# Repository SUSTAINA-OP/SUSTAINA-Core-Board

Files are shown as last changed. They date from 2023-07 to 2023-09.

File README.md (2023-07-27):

<html lang="en">

<head>
	<meta charset="uft-8">
	<meta name="author" content="Masato Kubotera">
    <meta name="description" content="">
</head>

<body>
    <p><strong>This product is currently under development!</strong></p>
	<h1>SUSTAINA Core Board</h1>
        <p>
			This product is the core electronic board of the open hardware platform humanoid robot SUSTAINA-OP<sup>TM</sup>.
			This product requires multiple modules(4 x <a href="https://github.com/SUSTAINA-OP/Power-Monitor-Module">Power Monitor Module</a> and 1 x <a href="https://github.com/SUSTAINA-OP/Buck-Boost-Switch-Mode-Power-Supply-Module">Buck-Boost Switch Mode Power Supply Module</a>) to work. The board automatically selects a priority power source from two battery inputs within the operating voltage range to supply various devices. The power input and output are equipped with short-circuit protection circuits using fuses. In addition, the battery input has multiple MOSFETs to prevent reverse connection and reverse current. The power supply to the actuator and single-board computer can be turned on and off with the load switch circuit.<br>
			<br>
			Rev. 1 of this product is used by <a href="https://github.com/citbrains">CIT Brains</a>, a participant in RoboCup2023 Soccer Humanoid League KidSize.
        </p>
	<h2>Features Rev. 1</h2>
        <p>
            <table>
                <tr>
                    <th>Top Surface of PCB</th>
                    <th>Bottom Surface of PCB</th>
                    <th>Assembled Electronic Components</th>
                </tr>
                <tr>
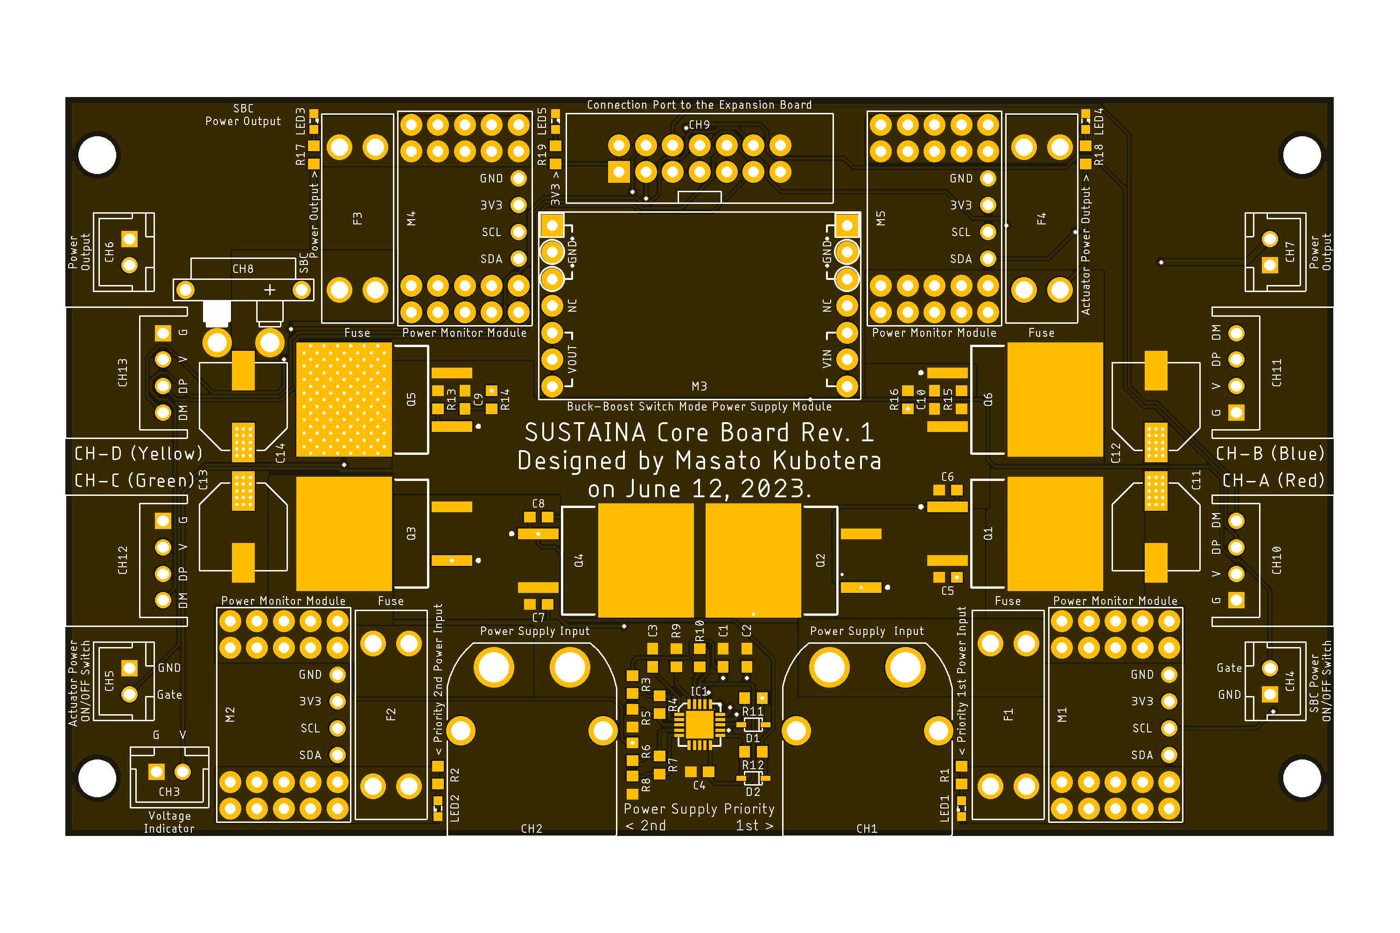
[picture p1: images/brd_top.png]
                    <td></td>
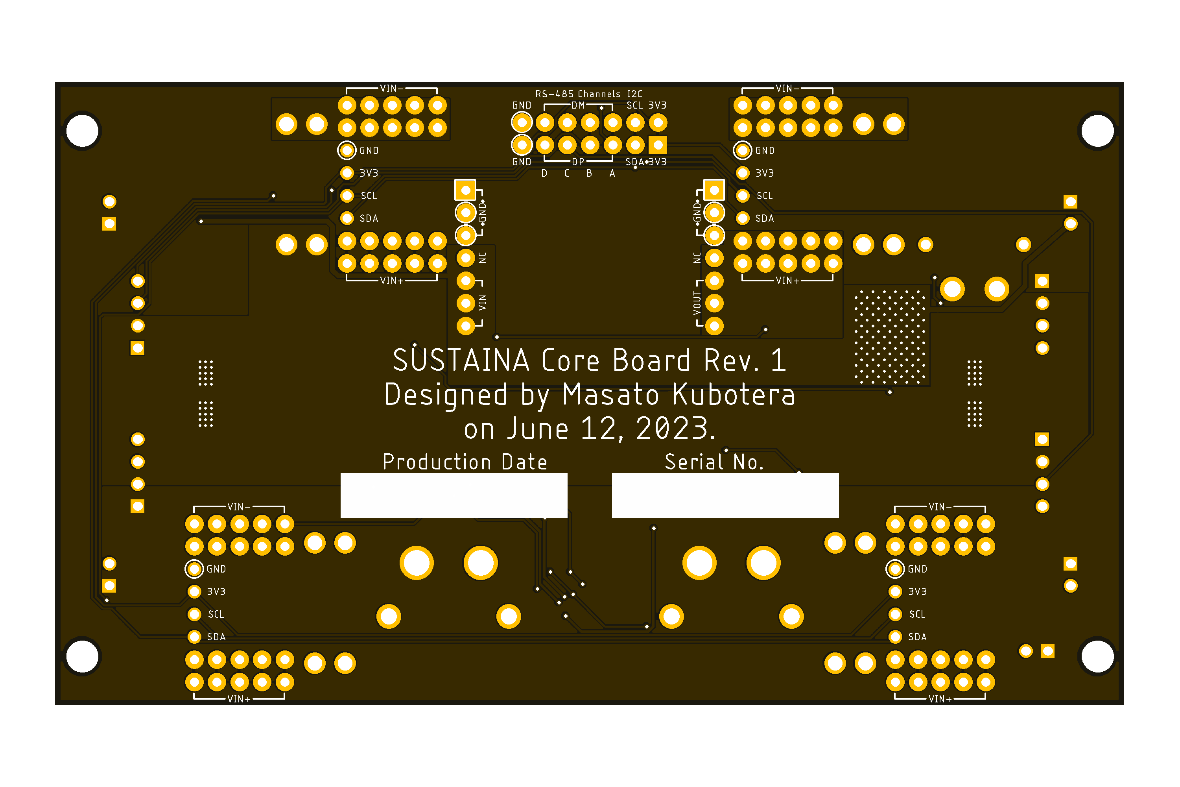
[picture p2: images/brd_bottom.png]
                    <td></td>
                    <td></td>
                </tr>
            </table>
        </p>
    <h3>PCB</h3>
        <p>
            <ul>
                <li>120 mm x 70 mm PCB layout</li>
                <li>4 x ø3.5 Mounting Holes</li>
            </ul>
        </p>
	<h2>Development Environments</h2>
    <p>
        This product is designed with the following software.
            <ul>
                <li><a href="https://www.autodesk.com/products/eagle/overview">Autodesk Eagle 9.6.2</a></li>
            </ul>
    </p>
    <h2>Repository Contents</h2>
        <p>
            <dl>
                <dt><a href="/images">\images</a></dt>
                <dd>PCB preview images and capture of design screen</dd>
                <dt><a href="/libraries">\libraries</a></dt>
                <dd>Libraries used in Autodesk Eagle design</dd>
                <dt><a href="/documents">\documents</a> </dt>
                <dd>Documentation for making and using this product</dd>
                <dt><a href="/pcb_order">\pcb_order</a> </dt>
                <dd>Gerber data and documentation for ordering PCB</dd>
                <dt><a href="/schematic.pdf">schematic.pdf</a></dt>
                <dd>Circuit diagram of this product</dd>
                <dt>*.brd</dt>
                <dd>Board wiring design file by Autodesk Eagle</dd>
                <dt>*.sch</dt>
                <dd>Circuit diagram design file by Autodesk Eagle</dd>
                <dt><a href="/.gitignore">.gitignore</a></dt>
                <dd>A file that tells Git not to track a particular file</dd>
                <dt><a href="/LICENSE">LICENSE</a></dt>
                <dd>License to use this product</dd>
            </dl>
        </p>
    <h2>Documentation</h2>
        <p>
            The following documents are available for this product.
            <ul>
                <li><a href="/pcb_order/README.md">\pcb_order\README.md</a>: Information for ordering the PCB</li>
                <li><a href="/documents/BOM.md">\document\BOM.md</a>: List of electronic components assembled on the PCB</li>
            </ul>
        </p>
    <h2>References</h2>
        <p>
            This product was designed with reference to the following products.
            <ul>
                <li></li>
            </ul>
        </p>
    <h2>Contact</h2>
        <p>
            If you have any questions, please contact the designer of this product, Masato Kubodera, by <a href="mailto:masato.kubotera@sustaina-op.com">e-mail</a>.<br>
            E-mail: <a href="mailto:masato.kubotera@sustaina-op.com">masato.kubotera@sustaina-op.com</a>
        </p>
    <h2>License Information</h2>
        <p>
            This product is open source. Please review the <a href="/LICENSE">LICENSE</a> for license information.<br>
            <br>
            This product by Masato Kubotera is licensed under a <a href="http://creativecommons.org/licenses/by-nc-sa/4.0/">Creative Commons Attribution-NonCommercial-ShareAlike 4.0 International License</a>.
        </p>    
</body>
</html>

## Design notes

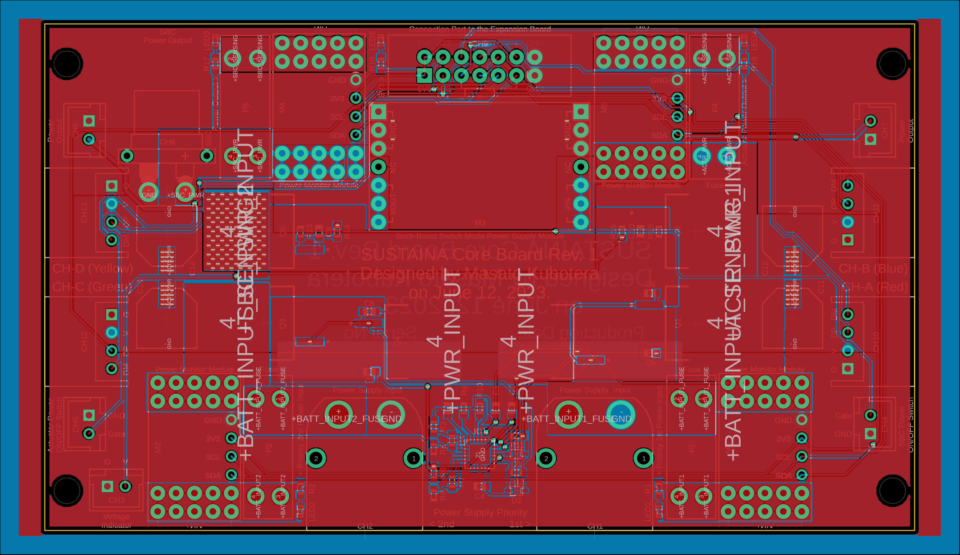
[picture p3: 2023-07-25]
images/brd.png

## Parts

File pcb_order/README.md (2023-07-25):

<html lang="en">

<head>
	<meta charset="uft-8">
	<meta name="author" content="Masato Kubotera">
    <meta name="description" content="">
</head>

<body>
	<h1>PCB Order</h1>
        <p>
            PCB/PCBA ordering were outsourced to <a href="https://www.elecrow.com/pcb-manufacturing.html">ELECROW</a>.<br>
            The following files were used to generate files for PCB/PCBA orders.
            <ul>
                <li>Eagle Design File:
                    <a href="https://www.elecrow.com/download/Elecrow_PCB_eagle_rule.zip">Elecrow_2-layer_PCB_eagle_rule.dru</a>
                </li>
                <li>Eagle CAM File:
                    <a href="https://www.elecrow.com/download/Elecrow_Gerber_Generater_DrillAlign.zip">Elecrow_Gerber_Generater_DrillAlign.cam</a>
                </li>
            </ul>
        </p>
    <h2>PCB Order Specifications</h2>
        <p>           
            <table>
                <tr>
                    <th>PCB Top Image</th>
                    <th>PCB Bottom Image</th>
                </tr>
                <tr>
                    <td></td>
                    <td></td>
                </tr>
            </table>
            The following  files used to order the PCB and their specifications. 
            <ul>
                <li>Gerber data: <a href="Gerber_date.zip">Gerber_date.zip</a></li>
            </ul>
            <details close>
                <summary>Click for more specifications</summary>
                <ul>
                    <li>Layers: 2</li>
                    <li>Dimension: 120 mm * 70 mm</li>
                    <li>Different Design: 1</li>
                    <li>PCB Thickness: 1.6</li>
                    <li>PCB Color: Matte Black</li>
                    <li>Surface Finish: HASL</li>
                    <li>Castellated Hole: No</li>
                    <li>Copper Weight: 2 oz</li>
                </ul>
            </details>
        </p>
    <h2>PCB Stencil Order Specifications</h2>
        <p>
                <details close>
                <summary>Click for more specifications</summary>
                <ul>
                    <li>Stencil type: Nom-Framework</li>
                    <li>Size (mm): 15cm X 15cm no frame</li>
                    <li>Stencil Side: Top</li>
                    <li>Mark point : No Fiducial</li>
                </ul>
            </details>
        </p>
    </body>
</html>

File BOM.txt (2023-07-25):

Qty Value                                      Device                                     Package                                    Parts                        Description                
2   0                                          R-US_R0603                                 R0603                                      R9, R10                      RESISTOR, American symbol  
7   0.1u                                       C-USC0603                                  C0603                                      C1, C2, C4, C5, C6, C7, C8   CAPACITOR, American symbol 
6   10k                                        R-US_R0603                                 R0603                                      R11, R12, R13, R14, R15, R16 RESISTOR, American symbol  
2   1180k                                      R-US_R0603                                 R0603                                      R3, R6                       RESISTOR, American symbol  
1   1n                                         C-USC0603                                  C0603                                      C3                           CAPACITOR, American symbol 
2   1u                                         C-USC0603                                  C0603                                      C9, C10                      CAPACITOR, American symbol 
5   2k                                         R-US_R0603                                 R0603                                      R1, R2, R17, R18, R19        RESISTOR, American symbol  
2   34k                                        R-US_R0603                                 R0603                                      R4, R7                       RESISTOR, American symbol  
4   3557-2                                     3557-2                                     3557-2                                     F1, F2, F3, F4                                          
4   35PFV150M8X10.5                            35PFV150M8X10.5                            35PFV150M8X10.5                            C11, C12, C13, C14                                      
2   86.6k                                      R-US_R0603                                 R0603                                      R5, R8                       RESISTOR, American symbol  
5   B2B-XH-A                                   B2B-XH-A                                   B2B-XH-A                                   CH3, CH4, CH5, CH6, CH7                                 
2   BAT54J,115                                 BAT54J,115                                 SOD-323-2                                  D1, D2                                                  
1   BUCK-BOOST-SWITCH-MODE-POWER-SUPPLY-MODULE BUCK-BOOST-SWITCH-MODE-POWER-SUPPLY-MODULE BUCK-BOOST-SWITCH-MODE-POWER-SUPPLY-MODULE M3                                                      
5   Green                                      LEDSML0603                                 SML0603                                    LED1, LED2, LED3, LED4, LED5 LED                        
1   HIF3FC-14PA-2.54DSA(71)                    HIF3FC-14PA-2.54DSA(71)                    HIF3FC-14PA-2.54DSA(71)                    CH9                                                     
1   LTC4418IUF                                 LTC4418IUF                                 LTC4418IUF                                 IC1                                                     
4   POWER-MONITOR-MODULE                       POWER-MONITOR-MODULE                       POWER-MONITOR-MODULE                       M1, M2, M4, M5                                          
4   S4B-XH-A                                   S4B-XH-A                                   S4B-XH-A                                   CH10, CH11, CH12, CH13                                  
6   SUM110P06-08L-E3                           SUM110P06-08L-E3                           TO-252-3                                   Q1, Q2, Q3, Q4, Q5, Q6                                  
1   XT30PW-F                                   XT30PW-F                                   XT30PW-F                                   CH8                                                     
2   XT60PW-M                                   XT60PW-M                                   XT60PW-M                                   CH1, CH2

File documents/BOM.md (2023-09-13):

<html lang="en">

<head>
	<meta charset="uft-8">
	<meta name="author" content="Masato Kubotera">
    <meta name="description" content="">
</head>

<body>
	<h1>BOM</h1>
        <p>
        The following electronic components are used for assembly on the PCB.
        <table>
                <tr>
                    <th>Top Designator</th>
                    <th>MFR.Part #</th>
                    <th>Distributor / Part #</th>
                    <th>Manufacturer</th>
                    <th>Part Detail</th>
                </tr>
                <tr>
                    <td>C1, C2, C4, C7, C8, C9, C10</td>
                    <td>GCM188L81H104K57</td>
                    <td><a href="https://akizukidenshi.com/catalog/g/gP-16143/">Akizuki / P-16143</a></td>
                    <td>Murata Electronics</td>
                    <td>Multilayer Ceramic Capacitor SMD 0.1uF 50V ±10% X8L 0603</td>
                </tr>
                <tr>
                    <td>C3</td>
                    <td>GRM188R72A102KA01D</td>
                    <td><a href="https://www.mouser.jp/ProductDetail/81-GRM18R72A102KA01D">Mouser / 81-GRM18R72A102KA01D</a></td>
                    <td>Murata Electronics</td>
                    <td>Multilayer Ceramic Capacitor SMD 1nF 100V ±10% X7R 0603</td>
                </tr>
                <tr>
                    <td>C5, C6</td>
                    <td>GRM188C81E105KA12</td>
                    <td><a href="https://akizukidenshi.com/catalog/g/gP-16993/">Akizuki / P-16993</a></td>
                    <td>Murata Electronics</td>
                    <td>Multilayer Ceramic Capacitor SMD 1uF 25V ±10% X6S 0603</td>
                </tr>
                <tr>
                    <td>CH1, CH2</td>
                    <td>XT60PW-M</td>
                    <td><a href="https://akizukidenshi.com/catalog/g/gC-18156/">Akizuki / C-18156</a></td>
                    <td><a href="https://www.china-amass.com/product/contain/1547q0bG8r4v98s7">Amass</a></td>
                    <td>High Current Board Connector - Male 35A 600V</td>
                </tr>
                <tr>
                    <td>CH3, CH4, CH5, CH6, CH7</td>
                    <td>B2B-XH-A</td>
                    <td><a href="https://akizukidenshi.com/catalog/g/gC-12247/">Akizuki / C-12247</a></td>
                    <td><a href="https://www.jst-mfg.com/product/pdf/eng/eXH.pdf">JST</a></td>
                    <td>XH Connector Header 2.5mm-pitch 2-position Top Entry</td>
                </tr>
                <tr>
                    <td>CH8</td>
                    <td>XT30PW-F</td>
                    <td><a href="https://akizukidenshi.com/catalog/g/gC-17948/">Akizuki / C-17948</a></td>
                    <td><a href="https://www.china-amass.com/product/contain/7U1GeR54529k3260">Amass</a></td>
                    <td>High Current Board Connector - Male 20A 500V</td>
                </tr>
                <tr>
                    <td>CH9</td>
                    <td>HIF3FC-14PA-2.54DSA(71)</td>
                    <td><a href="https://www.mouser.jp/ProductDetail/798-HIF3FC14PA254D71">Mouser / 798-HIF3FC14PA254D71</a></td>
                    <td>Hirose Connector</td>
                    <td>Low Profile Connector 2.54mm-pitch 14-position Straight Type Pin Header</td>
                </tr>
                <tr>
                    <td>CH10, CH11, CH12, CH13</td>
                    <td>S4B-XH-A(LF)(SN)</td>
                    <td><a href="https://akizukidenshi.com/catalog/g/gC-12842/">Akizuki / C-12842</a></td>
                    <td><a href="https://www.jst-mfg.com/product/pdf/eng/eXH.pdf">JST</a></td>
                    <td>XH Connector Header 2.5mm-pitch 4-position Side Entry</td>
                </tr>
                <tr>
                    <td>F1, F2, F3, F4</td>
                    <td>3557-2</td>
                    <td><a href="https://www.mouser.jp/ProductDetail/534-3557-2">Mouser / 534-3557-2</a></td>
                    <td>Keystone Electronics</td>
                    <td>Fuse Holder 500V 30A</td>
                </tr>
                <tr>
                    <td>IC1</td>
                    <td>LTC4418IUF</td>
                    <td><a href="https://www.mouser.jp/ProductDetail/584-LTC4418IUFPBF">Mouser / LTC4418IUF#PBF</a></td>
                    <td><a href="https://www.analog.com/en/products/ltc4418.html">Analog Devices</a></td>
                    <td>Dual Channel Prioritized PowerPath Controller SMD QFN-20</td>
                </tr>
                <tr>
                    <td>LED1, LED2, LED3, LED4, LED5</td>
                    <td>150060VS86000</td>
                    <td><a href="https://www.mouser.jp/ProductDetail/710-150060VS86000">Mouser / 710-150060VS86000</a></td>
                    <td><a href="https://www.we-online.com/components/products/datasheet/150060VS86000.pdf">Wurth Elektronik</a></td>
                    <td>Standard LED SMD 2V 20mA GREEN 573nm 0603</td>
                </tr>
                <tr>
                    <td>M1, M2, M4, M5</td>
                    <td>Power Monitor Module Rev.2</td>
                    <td><a href="https://github.com/SUSTAINA-OP/Power-Monitor-Module">Custom Board - SUSTAINA-OP / Power-Monitor-Module</a></td>
                    <td>-</td>
                    <td></td>
                </tr>
                <tr>
                    <td>M3</td>
                    <td>Buck-Boost Switch Mode Power Supply Module Rev.1</td>
                    <td><a href="https://github.com/SUSTAINA-OP/Buck-Boost-Switch-Mode-Power-Supply-Module">Custom Board - SUSTAINA-OP / Buck-Boost-Switch-Mode-Power-Supply-Module</a></td>
                    <td>-</td>
                    <td></td>
                </tr>
                <tr>
                    <td>Q1, Q2, Q3, Q4, Q5, Q6</td>
                    <td>SUM110P06-08L-E3</td>
                    <td><a href="https://www.mouser.jp/ProductDetail/781-SUM110P06-08L-E3">Mouser / 781-SUM110P06-08L-E3</a></td>
                    <td>Vishay</td>
                    <td>P-channel MOSFET SMD 60V 110A 272W 8.0Ω TO-263-3</td>
                </tr>
                <tr>
                    <td>R1, R2, R4, R7, R17, R18, R19</td>
                    <td>RC0603FR-102KL</td>
                    <td><a href="https://www.mouser.jp/ProductDetail/603-RC0603FR-102KL">Mouser / 603-RC0603FR-102KL</a></td>
                    <td>YAGEO</td>
                    <td>Thick Film Resistor SMD 2kΩ 1/10W ±1% 0603</td>
                </tr>
                <tr>
                    <td>R3, R6</td>
                    <td>RC0603FR-1018KL</td>
                    <td><a href="https://www.mouser.jp/ProductDetail/603-RC0603FR-1018KL">Mouser / 603-RC0603FR-1018KL</a></td>
                    <td>YAGEO</td>
                    <td>Thick Film Resistor SMD 18kΩ 1/10W ±1% 0603</td>
                </tr>
                <tr>
                    <td>R5, R8</td>
                    <td>RC0603FR-101KL</td>
                    <td><a href="https://www.mouser.jp/ProductDetail/603-RC0603FR-101KL">Mouser / 603-RC0603FR-101KL</a></td>
                    <td>YAGEO</td>
                    <td>Thick Film Resistor SMD 1kΩ 1/10W ±1% 0603</td>
                </tr>
                <tr>
                    <td>R9, R10</td>
                    <td>RC0603FR-130RL</td>
                    <td><a href="https://www.mouser.jp/ProductDetail/603-RC0603FR-130RL">Mouser / 603-RC0603FR-130RL</a></td>
                    <td>YAGEO</td>
                    <td>Thick Film Resistor SMD 0Ω 1/10W ±1% 0603</td>
                </tr>
                <tr>
                    <td>R13, R14, R15, R16</td>
                    <td>RC0603FR-1010KL</td>
                    <td><a href="https://www.mouser.jp/ProductDetail/603-RC0603FR-1010KL">Mouser / 603-RC0603FR-1010KL</a></td>
                    <td>YAGEO</td>
                    <td>Thick Film Resistor SMD 10kΩ 1/10W ±1% 0603</td>
                </tr>
            </table>
            The following are electronic components of DNP (Do Not Populate).
            <table>
                <tr>
                    <th>Top Designator</th>
                    <th>MFR.Part #</th>
                    <th>Distributor / Part #</th>
                    <th>Manufacturer</th>
                    <th>Part Detail</th>
                </tr>
                <tr>
                    <td>C11, C12, C13, C14</td>
                    <td>35PFV150M8X10.5</td>
                    <td><a href="https://akizukidenshi.com/catalog/g/gP-14492/">Akizuki / P-14492</a></td>
                    <td>Rubycon</td>
                    <td>Aluminum Organic Polymer Capacitor SMD 150uF 35V 20% PFV AEC-Q200</td>
                </tr>
                <tr>
                    <td>D1, D2</td>
                    <td>BAT54J,115</td>
                    <td><a href="https://www.mouser.jp/ProductDetail/771-BAT54J115">Mouser / 771-BAT54J115</a></td>
                    <td>Nexperia</td>
                    <td>Schottky barrier single diode SMD 30V 200mA SOD323F</td>
                </tr>
                <tr>
                    <td>R11, R12</td>
                    <td>RC0603FR-1010KL</td>
                    <td><a href="https://www.mouser.jp/ProductDetail/603-RC0603FR-1010KL">Mouser / 603-RC0603FR-1010KL</a></td>
                    <td>YAGEO</td>
                    <td>Thick Film Resistor SMD 10kΩ 1/10W ±1% 0603</td>
                </tr>
            </table>
        </p>
</body>
</html>

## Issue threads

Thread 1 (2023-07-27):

SBC電源に高負荷が接続されている際にバッテリー切り替えができない

MasatoKubotera, 2023-07-27:
SUSTAINA CoreBoardは，Buck-Boost Switch Mode Power Supply Module：https://github.com/SUSTAINA-OP/Buck-Boost-Switch-Mode-Power-Supply-Module を通じでシングルボードコンピュータに電源を供給している．

シングルボードコンピュータに高負荷が接続されているとき（例：SUSTAINA-OPにおいて，GPU処理を伴う戦略起動時）にバッテリ（満充電）のみ及びスイッチングを用いた切り替えいずれにおいても切り替えができない事象が生じている．切り替えに失敗するときは，シングルボードコンピュータがの電源が落ちている（強制シャットダウン）状態である．

RoboCup 2023ではバッテリ切り替え時は，高負荷ではない状態で行うことで回避していた．

MasatoKubotera, 2023-07-27:
SBC電源電圧は18.5V程度であり，シングルボードコンピュータの動作電圧範囲９～１９V@３Aである．
https://www.switch-science.com/products/7932

電圧降下によってシャットダウンしている場合は，１０V近く電圧降下していることになる．

MasatoKubotera, 2023-09-13:
以下のIssueの内容でここで問題視しているものは解決した．
https://github.com/SUSTAINA-OP/SUSTAINA-Core-Board/issues/11

Closed 2023-09-13.

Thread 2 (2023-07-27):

アクチュエータ電源押下時にSBCの電源が落ちることがある

MasatoKubotera, 2023-07-27:
一部のSUSTAINA-OPにおいて，アクチュエータ電源押下時にSBCの電源が落ちることがある．

MasatoKubotera, 2023-07-30:
ボード上のINA226のログからアクチュエータ電源投下時にSBC電源が3.68Vまで降下していることが分かった．

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

MasatoKubotera, 2023-07-30:
バッテリーからの供給際には，SBC電源が落ちることは無かった．

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

MasatoKubotera, 2023-07-30:
上記二つの測定ソースコード
以下のコードで電流値を抜いたもの．

https://github.com/SUSTAINA-OP/SUSTAINA-Core-Board/tree/Rev1/firmware
```.ino
#include "./src/INA226.h"
#include "Wire.h"

// number of sensors to be mounted
const int numSensors = 4;

// array of sensor objects
INA226 sensors[numSensors] = {
  INA226(0x40),
  INA226(0x41),
  INA226(0x42),
  INA226(0x43)
};

void setup()
{
  Serial.begin(115200);
  Wire.begin();

  for (int i = 0; i < numSensors; i++)
  {
    if (!sensors[i].begin())
    {
      Serial.println("Could not connect to sensor. Fix and Reboot");
      while (1);
    }
    sensors[i].setMaxCurrentShunt(20, 0.002);
  }
}

void loop()
{
  for (int i = 0; i < numSensors; i++)
  {
    printSensorData(sensors[i]);
    Serial.print(i < numSensors - 1 ? ",": "\n");
  }
  delay(1);
}

void printSensorData(INA226 & sensor)
{
  String address = String(sensor.getAddress(), HEX);
  Serial.print("0x" + address + ":");
  Serial.print(sensor.getBusVoltage());
  /*
  Serial.print(",");
  Serial.print("CURRENT_0x" + address + ":");
  Serial.print(sensor.getCurrent_mA());
  */
}

```

MasatoKubotera, 2023-07-30:
以下，追加検証したときのプロット

スイッチング電源

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

バッテリー時
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

MasatoKubotera, 2023-07-30:
スイッチング電源を接続したときの電圧電流グラフ
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

MasatoKubotera, 2023-07-30:
バッテリー電源を接続したときの電圧電流グラフ
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

MasatoKubotera, 2023-07-30:
バッテリー，スイッチング電源共に，SBC電源範囲を下回る電圧降下がみられている・

MasatoKubotera, 2023-08-26:
アクチュエータ電源投下時に正常にアクチュエータの内部MCUが起動しないことがあった．
電源立ち上がりについて近藤に問い合わせた．
以下，やり取り【外部秘】
https://docs.google.com/document/d/1ASpvD2zdjgcxrFOtTs4T46jRfEMR--8DcKEUh9-CHbw/edit?usp=sharing

MasatoKubotera, 2023-09-06:
平滑用コンデンサを除去し，スロースタートのRC回路構成を回路図通りに戻したことにより，電圧降下が小さくなった．
また，突入電流による電圧降下が起きた際に電源有効判定により電源が遮断されないようになった．

- https://github.com/SUSTAINA-OP/SUSTAINA-Core-Board/issues/8
- https://github.com/SUSTAINA-OP/SUSTAINA-Core-Board/issues/5

これにより，アクチュエータ電源押下時にSBCの電源が落ちることがなくなったと考えられる．

Closed 2023-09-13.

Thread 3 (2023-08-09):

デュアル・チャネル優先順位付けPowerPathコントローラによる突入電流防止回路の設計ミス

MasatoKubotera, 2023-08-09:
LTC4418のサンプル回路を組み込んでいるが，以下の点で設計ミスがあった．

CS，CVS共に0.1uFを実装しているが，要件として 10*CS≦CVSがあった．

>LTC4418では、出力電圧をスルーレートで制限することによって突入電流を低減することができます。ゲート・ドライバは、図4に示すように、抵抗、コンデンサ、およびショットキ・ダイオードを使用して、出力電圧をスルーレートで制限するように構成することができます。直列の抵抗RSとコンデンサCSは突入電流の制限部品ですが、ショットキ・ダイオードDSは、G1の電圧がVS1の電圧に達すると高速のターンオフ経路になります。CSは外付けPチャネルMOSFETの逆伝達容量CRSS(MAX)の10倍以上になるように、またCVSはCSの10倍になるように選択します。あるいは、CRSS(MAX)自体をCSの代わりに使用することができます。ただし、その値はVDSの電圧が最小のときの値です

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

MasatoKubotera, 2023-08-09:
Rev.1 で実装しているFETの**Reverse Transfer Capacitance Crss**は900pFであった．
https://www.vishay.com/docs/72439/sum110p06-07l.pdf#page=2

CSは，0.1uFを実装しているので，CRSS(MAX)の10倍以上という指定には当てはまっている．

MasatoKubotera, 2023-09-06:
C_VSに対応するのは，Rev.1では，C5，C7の0.1uF．
これを，CS（C6，C8=0.1uF）の10倍以上なので，1uF以上を実装する必要あり．

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

Closed 2023-09-13.

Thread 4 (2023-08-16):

FETの置換

MasatoKubotera, 2023-08-16:
小型または消費電力(損失)の小さいFETに置き換えたい．

SUSTAINA-Core-Board Rev. 1（RoboCup2023）
https://www.mouser.jp/ProductDetail/781-SUM110P06-08L-E3

Main Board Ver. 2.2（RoboCup2022）
https://www.mouser.jp/ProductDetail/78-SQM40P10-40L_GE3

MasatoKubotera, 2023-08-16:
候補

https://www.mouser.jp/ProductDetail/78-SQM40041EL_GE3
Rds On - Drain-Source Resistance:	33 mOhms
Pd - Power Dissipation:	150 W

https://www.mouser.jp/ProductDetail/781-SI7997DP-T1-GE3
Rds On - Drain-Source Resistance:	5.5 mOhms
Pd - Power Dissipation:	46 W
**2 Channel**

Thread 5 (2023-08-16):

パワーアップコンデンサ・平滑用コンデンサについて考える

MasatoKubotera, 2023-08-16:
https://www.kopropo.co.jp/blogs/view/151
https://blog.goo.ne.jp/pook24/e/085a751e153f50b751561a5663658512

MasatoKubotera, 2023-08-16:
MainBoard Ver. 2.2，SUSTAINA Core Board Rev .1共にソフトスタート（突入電流防止のロードスイッチ）が組み込まれており，そのスイッチ後に大容量コンデンサを実装している．

これらのコンデンサは電源投入後に充電時間を要する．
そのため，ソフトスタートで設定した値よりも一定電圧になるまで時間を要し，サーボモータの内部MCUの起動時間内に基準電圧まで立ち上がらないことが発生している．

しかし，これらのパワーアップコンデンサは，アクチュエータの駆動時の電圧降下を抑えるために重要な働きを有するため，安易に外すことができないものである．

https://github.com/MasatoKubotera/MainBoard_ver2_2/blob/master/Schematic.pdf
https://github.com/SUSTAINA-OP/SUSTAINA-Core-Board/blob/Rev1/schematic.pdf

MasatoKubotera, 2023-08-16:
アクチュエータ駆動時の電圧降下に関しては，ロギングシステムが完成したら容易に可視化できるようになるかもしれない．

MasatoKubotera, 2023-09-03:
アクチュエータ内部の電源供給部に25V-100uFの電解コンデンサが取り付けられることが分かった．
そのため，SUSTAINA-Core-Borad上にパワーアップコンデンサ・平滑コンデンサは不要かもしれない．

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

※故障基板のため，B3Mの３種の内型番不明

MasatoKubotera, 2023-09-06:
C11，C12，C13，C14：150uFのアクチュエータ電源平滑用のコンデンサ類をすべて取り外して検証した．
https://github.com/citbrains/sustaina-log/issues/20

電圧波形などは確認していないが，フィールドでサッカー競技（歩く，蹴る）ができることを確認した．

Closed 2023-09-13.

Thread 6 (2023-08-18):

アクチュエータに安定した電力を供給する

MasatoKubotera, 2023-08-18:
現状，アクチュエータにはバッテリ電圧がそのまま（寄生ダイオードなどにより電圧降下はある）印可されており，バッテリー残量に応じて電圧が変動する．

アクチュエータのトルク及び回転速度は，電圧によって変化するため，
現状使用しているバッテリー（LiHv 3S1P 2800mAh）では，最大１３．０５Vから１１．１Vまで駆動し，その電圧差分は約２Vである．

これにより，競技開始直後と終了間際では，歩行制御の挙動が変わる恐れがある．

そのため，アクチュエータに供給する電圧を一定にすることで終始変わらない安定性を実現したい．

MasatoKubotera, 2023-08-18:
参考：Bit-Botsによる降圧DCDC [i7A4W033A033V-0C1-R](https://product.tdk.com/en/search/power/switching-power/dc-dc-converter/info?part_no=i7A4W033A033V-0C1-R)を用いた[Wolfgang Constant Voltage](https://doku.bit-bots.de/meta/manual/hardware/electronics/wolfgang_constant_voltage.html)

MasatoKubotera, 2023-08-18:
KONDOのB3Mおよび後継のPMXシリーズの公称電圧は１２V

バッテリ電圧範囲１３．０５Vから１１．１V内であるため，同バッテリを用いる場合には，昇降圧である必要がある．

候補
i7Cシリーズ
https://product.tdk.com/system/files/dam/doc/product/power/switching-power/dc-dc-converter/catalog/i7c_j.pdf

i7C4W012A050V-0C1-R　ベースプレート付
https://product.tdk.com/ja/search/power/switching-power/dc-dc-converter/info?part_no=i7C4W012A050V-0C1-R

i7C4W012A050V-0F1-R　ヒートシンク付
https://product.tdk.com/ja/search/power/switching-power/dc-dc-converter/info?part_no=i7C4W012A050V-0F1-R

MasatoKubotera, 2023-08-26:
https://industrial.panasonic.com/jp/ss/technical/b13

MasatoKubotera, 2023-09-03:
評価キット
i7C12A-C03-EVK-S1
https://product.tdk.com/en/search/power/switching-power/pwr-acc/info?part_no=i7C12A-C03-EVK-S1

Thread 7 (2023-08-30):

12V電源系とシングルボードコンピュータとの通信接続を絶縁仕様にする

MasatoKubotera, 2023-08-30:
SUSTAINA-Core-Board故障時，以下2つのモジュールを通じてシングルボードコンピュータも損傷する恐れがあるため，通信を絶縁仕様にする

電力計測モジュール
https://github.com/SUSTAINA-OP/Power-Monitor-Module

USB to Quad RS-485 Conv. Module
https://github.com/SUSTAINA-OP/USB-to-Quad-RS-485-Conv-Module

MasatoKubotera, 2023-08-30:
チップ候補

ADM3260
https://www.analog.com/jp/products/adm3260.html
ADM3260 I2Cアイソレータモジュール(絶縁+電源)
https://strawberry-linux.com/catalog/items?code=23260

MAX14933【新規設計にお薦めします】
https://www.analog.com/jp/products/max14933.html

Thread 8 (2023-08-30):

スイッチング電源利用時にアクチュエータに負荷がかけれない

MasatoKubotera, 2023-08-30:
アクチュエータ出力に１5Aの負荷をかけると，
入力直後のバックトゥバックのPch FETが駆動が不安定になることが確認できた．

これにより，２０A以上の負荷をかけた場合でも
ロードスイッチ用途のFETにゲートがオンになるまでの電圧にならない．
よって，短絡などが起きたとしても，出力側に搭載している２０Aヒューズが切れることが無いことが分かった．

また，この問題はスイッチング電源利用時にアクチュエータがしようできないことも関与している．

MasatoKubotera, 2023-09-03:
問題個所

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

MasatoKubotera, 2023-09-03:
検証は，以下で指摘しているコンデンサの値違いは修正した基板を用いている．
[デュアル・チャネル優先順位付けPowerPathコントローラによる突入電流防止回路の設計ミス #3](https://github.com/SUSTAINA-OP/SUSTAINA-Core-Board/issues/3)
C7 : 0.1uf -> 1uF

MasatoKubotera, 2023-09-03:
アクチュエータ出力に１５A負荷をつないだとき

青：G2
黄：+POWER_INPUT
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

MasatoKubotera, 2023-09-03:
PowerPathコントローラで制御しているFET周りをシンプルにして検証してみた

C6,R11,D1を取り外し，G1とG1_をショートさせた

青：+POWER_INPUT
黄：G1
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

MasatoKubotera, 2023-09-03:
電源：12V20A　スイッチング電源No.6

青：+POWER_INPUT
黄：+BATT_INPUT_SENSING1

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

MasatoKubotera, 2023-09-03:
OU/OV設定用の抵抗構成が
1180k-34k-86.6k
の時は，
10.784V以下の時にシャットダウンする．

下図の波形から負荷がかかったことによる電圧降下によってOU電圧が下回りシャットダウンしている恐れがある

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

http://beta-tools.analog.com/ltpowertools/LTC4418/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

MasatoKubotera, 2023-09-03:
電源：ハイペリオン バッテリー　１１．６V

電源をバッテリーにすることで１５Aの負荷をかけも電圧降下しないことが分かった．

青：+POWER_INPUT
黄：+BATT_INPUT_SENSING1

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

![image]()

MasatoKubotera, 2023-09-03:
スイッチング電源を用いてアクチュエータ駆動ができないのは，UVを下回ることがあり得るから．

そもそも，スイッチング電源入力にUVが必要なのか？

MasatoKubotera, 2023-09-03:
UV/OV について，設定しないということはできなそう．

下限は，SBC電源用のスイッチング電源入力電圧を参考に決めてよさそう．

https://github.com/SUSTAINA-OP/Buck-Boost-Switch-Mode-Power-Supply-Module

UV 5V，OV15Vととして，
12k-2k-1kの組み合わせとりあえず組みと，１５Aでも駆動しそう．

スイッチング電源
１０A負荷
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

１５A負荷
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

２０A負荷
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

[LTC4418 PowerPath Controller Design Tool](http://beta-tools.analog.com/ltpowertools/LTC4418/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)

MasatoKubotera, 2023-09-06:
以下，検証でスイッチング電源を利用してアクチュエータが利用できることを確認した．

- https://github.com/citbrains/sustaina-log/issues/20

Closed 2023-09-13.

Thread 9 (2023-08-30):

検証用Arduino用で3A以上が計測出来ない

MasatoKubotera, 2023-08-30:
現状公開している，https://github.com/RobTillaart/INA226 を用いたファームウェアで，電流計測が正常に行えないことを確認した．

別のライブラリ：https://github.com/asukiaaa/INA226_asukiaaa を使用することで計測できることは確認しているので，ライブラリの問題の可能性が高い．

hiroki-0001, 2024-06-05:
こちら，確認しました．

https://github.com/RobTillaart/INA226 のサンプルコードの[INA226_demo.ino](https://github.com/RobTillaart/INA226/blob/master/examples/INA226_demo/INA226_demo.ino)を使用しました．

安定化電源(KX-100L)と直流電子負荷装置(Maynuo M9711)を用いて，電流は5Aをかけて，電流値を確認したところ，以下のように電流が，3276.7mAで最大となり，それ以上は計測できませんでした．

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

同様の構成で，https://github.com/asukiaaa/INA226_asukiaaaのサンプルコードの[printVoltageAndCurrent](https://github.com/asukiaaa/INA226_asukiaaa/blob/master/examples/printVoltageAndCurrent/printVoltageAndCurrent.ino)で確認すると，5Aでも計測することが出来ました．(誤差は多少ありますが)

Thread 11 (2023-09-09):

LTC4418のUV/OVについて考える

MasatoKubotera, 2023-09-09:
LTC4418
https://www.analog.com/jp/products/ltc4418.html#product-overview

では，入力過電圧/低電圧保護のために閾値電圧を複数の抵抗によって設定できる．

ここでは，閾値電圧の設定について考える．

MasatoKubotera, 2023-09-09:
以下の電圧波形は，スイッチング電源とバッテリーの２電源を接続し，スイッチング電源を抜いた時の波形である．
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

Ch1 黄色：VS1
Ch2 水色：+SBC_PWR
Ch3 赤色：+SBC_PWR_INPUT
Ch4 青色：+ACTR_PWR

基板は，Rev.1の改造版である．改造内容は以下を参照．
https://github.com/citbrains/sustaina-log/issues/20#issue-1883722557

12k-2k-1kの抵抗構成で，UV:5V，OV:15として設定されている．

UV:５Vとして設定されているため，優先順位2位のバッテリに切り替えられるのはこの電圧を下回った時である．
しかし，この時同時に，Buck-Boost Switch Mode Power Supply Moduleの動作電圧を下回っているため，シングルボードコンピュータへの供給電源（+SBC_PWR）も降下していることがわかる．
https://github.com/SUSTAINA-OP/Buck-Boost-Switch-Mode-Power-Supply-Module

これらより，UVはBuck-Boost Switch Mode Power Supply Moduleの動作範囲を下回らないように設定する必要がある．

MasatoKubotera, 2023-09-11:
戦略負荷をかけていない時の波形
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

MasatoKubotera, 2023-09-11:
抵抗
18k-2k-1k
UV:7V, OV:21

戦略起動中にスイッチング電源を抜いてバッテリに切り替え
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

戦略かけた時にスイッチング電源を挿してバッテリから切り替え
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

MasatoKubotera, 2023-09-11:
抵抗
18k-2k-1k
UV:7V, OV:21
に変更

**Ch1 黄色：+BATT_INPUT_SENSING1**
Ch2 水色：+SBC_PWR
Ch3 赤色：+SBC_PWR_INPUT
**Ch4 青色：+BATT_INPUT_SENSING2**

戦略起動中にスイッチング電源を抜いてバッテリに切り替え②➤Jetsonが落ちた
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
戦略かけた時にスイッチング電源を挿してバッテリから切り替え➤Jetsonが落ちた
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

MasatoKubotera, 2023-09-11:
戦略起動中にスイッチング口のバッテリを抜いてバッテリに切り替え➤Jetsonが落ちた
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

戦略かけた時にスイッチング口にバッテリを挿してバッテリ口のバッテリから切り替え➤Jetsonが落ちなかった
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

MasatoKubotera, 2023-09-13:
上記の問題で切り替えができないのは，
電源の電源の検証有効時間が過ぎて，FETのゲートに電圧が印加されたと同時に，
接続されていた方のゲートが切断されるからである．

この時に，Buck to Buckで構成されたFETがソフトスタートされるため，一定電圧になるまでに時間を要す．
そのため，一時的に電圧が降下するため，切り替えが失敗している可能性がある．

MasatoKubotera, 2023-09-13:
Rev 1.1としてSchematicを変更した．

変更前
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

変更後
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

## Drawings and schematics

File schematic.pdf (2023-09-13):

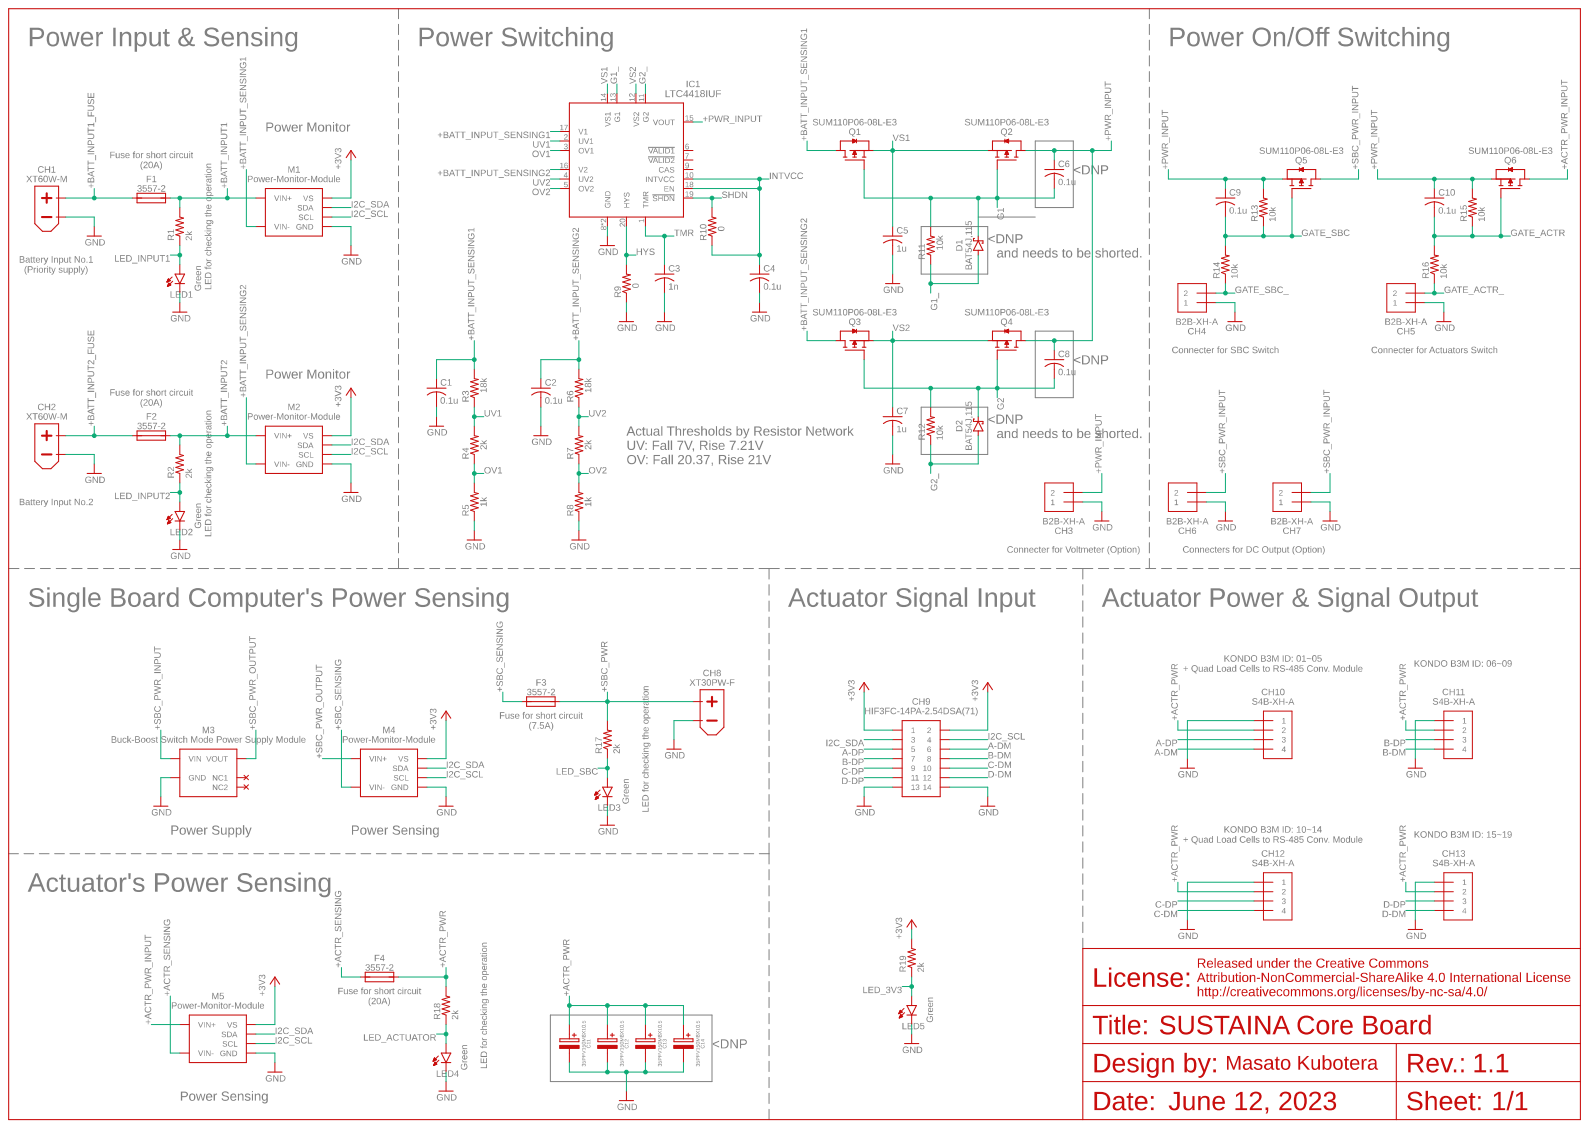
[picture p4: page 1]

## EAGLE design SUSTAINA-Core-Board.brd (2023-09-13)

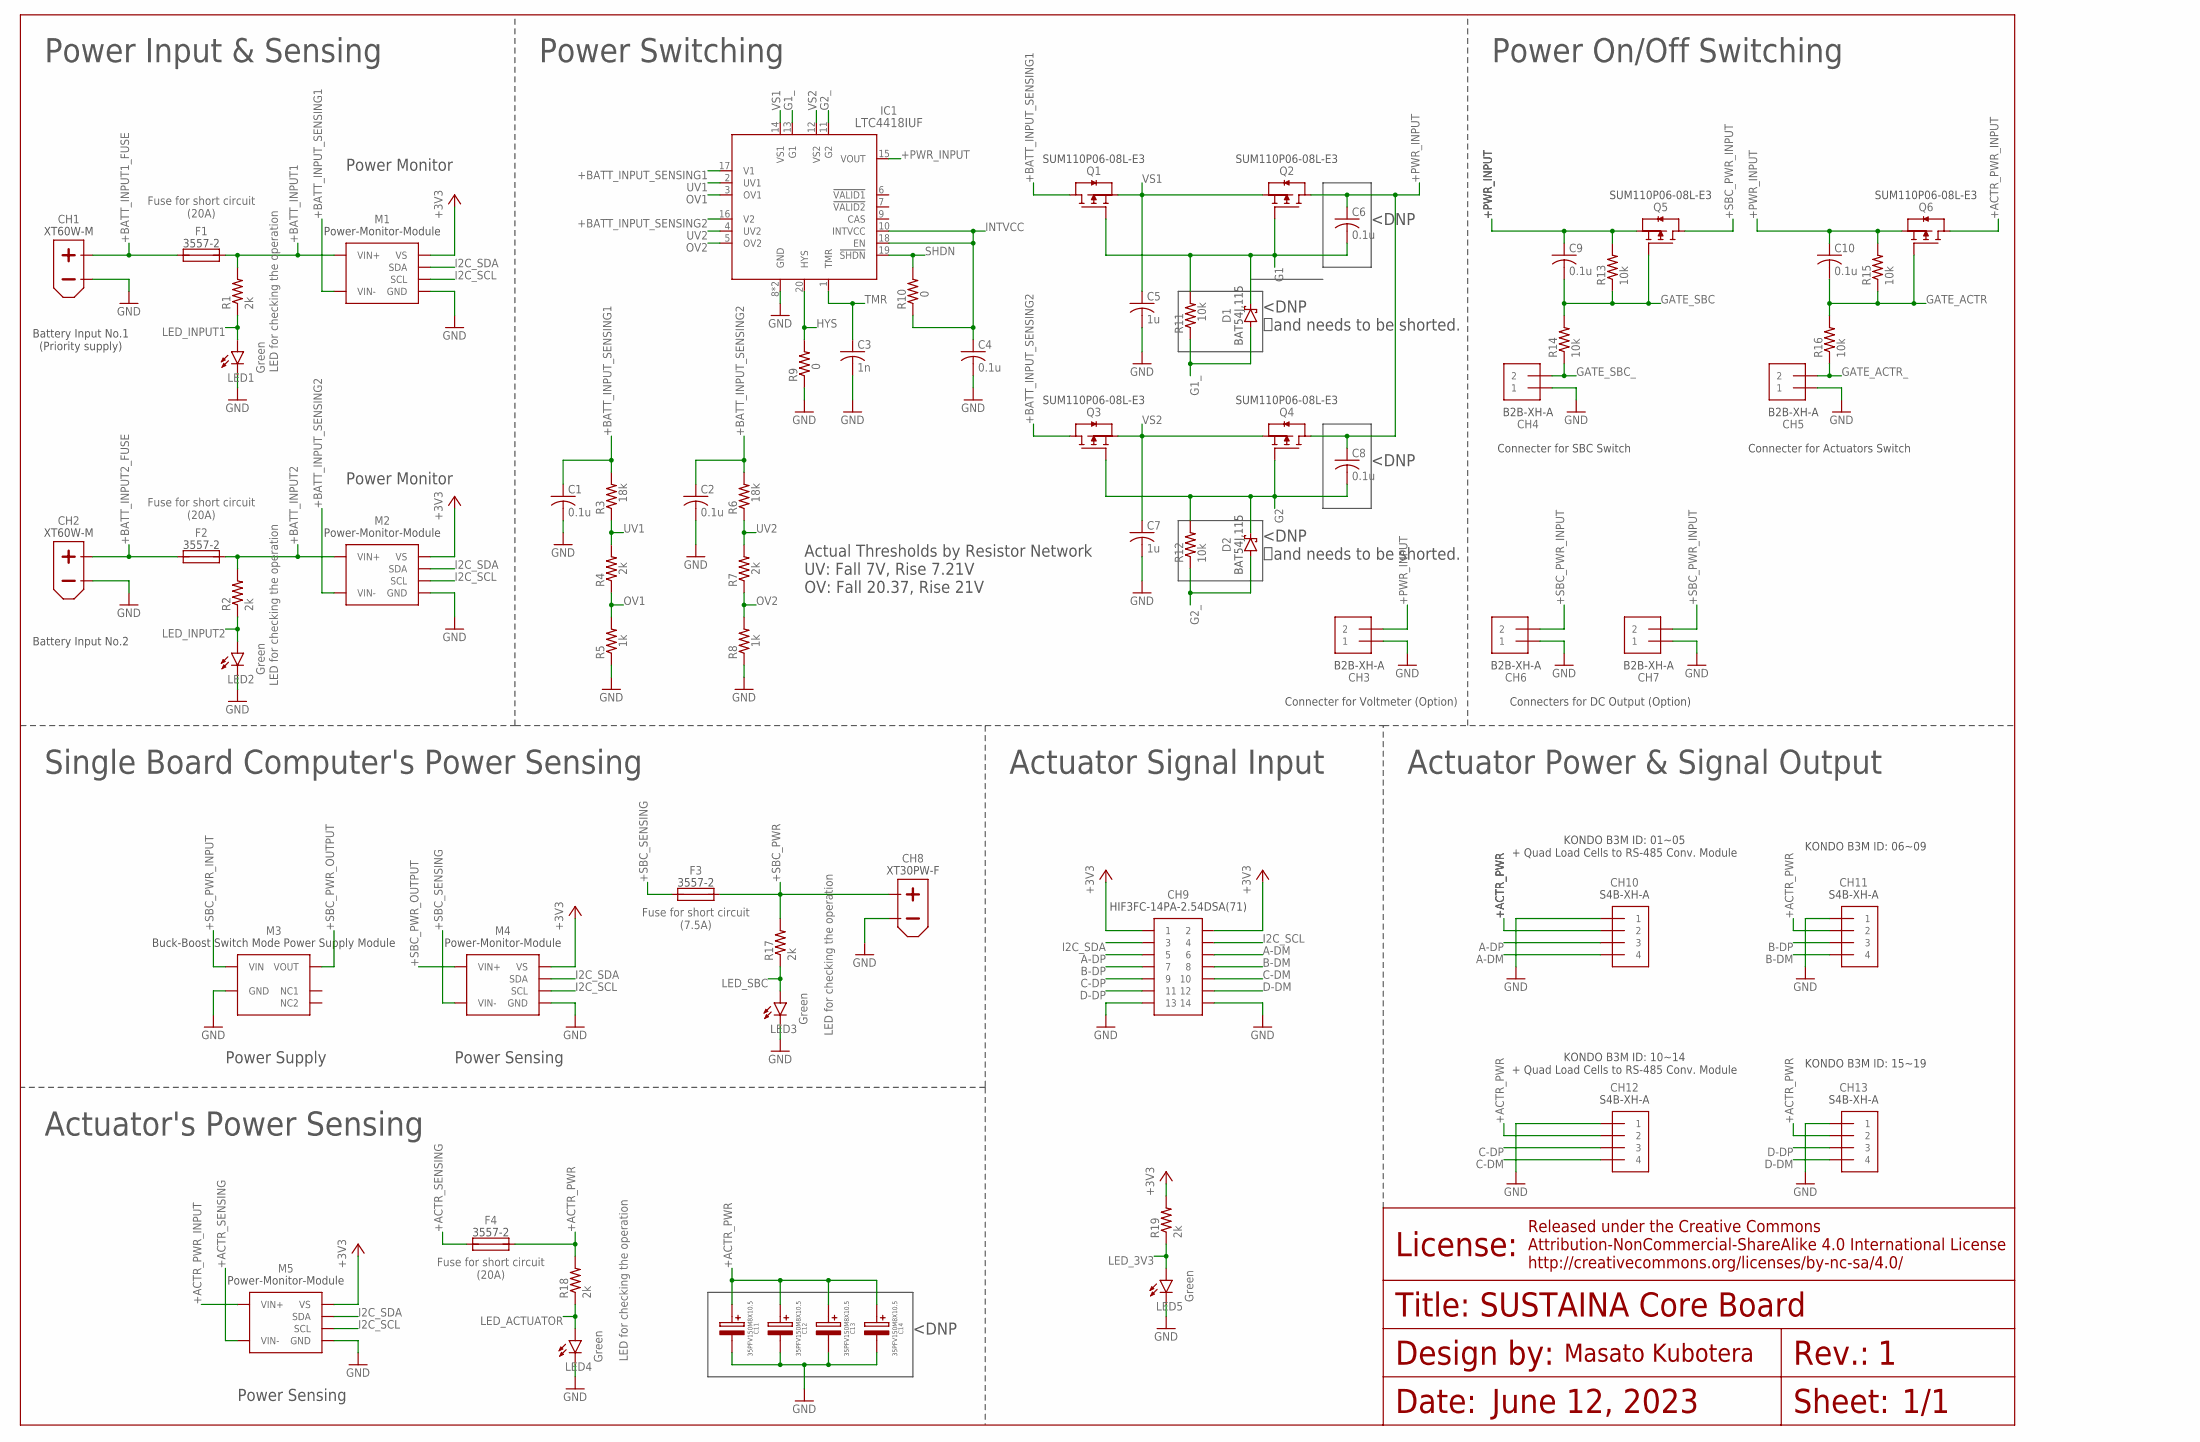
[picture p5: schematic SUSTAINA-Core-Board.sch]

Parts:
C1, C2, C4, C6, C8, C9, C10: 0.1u; C0603
C3: 1n; C0603
C5, C7: 1u; C0603
C11, C12, C13, C14: 35PFV150M8X10.5
CH1, CH2: XT60PW-M
CH3, CH4, CH5, CH6, CH7: B2B-XH-A
CH8: XT30PW-F
CH9: HIF3FC-14PA-2.54DSA(71)
CH10, CH11, CH12, CH13: S4B-XH-A
D1, D2: BAT54J,115; SOD-323-2
F1, F2, F3, F4: 3557-2
IC1: LTC4418IUF
LED1, LED2, LED3, LED4, LED5: Green; SML0603
M1, M2, M4, M5: POWER-MONITOR-MODULE
M3: BUCK-BOOST-SWITCH-MODE-POWER-SUPPLY-MODULE
Q1, Q2, Q3, Q4, Q5, Q6: SUM110P06-08L-E3; TO-252-3
R1, R2, R4, R7, R17, R18, R19: 2k; R0603
R3, R6: 18k; R0603
R5, R8: 1k; R0603
R9, R10: 0; R0603
R11, R12, R13, R14, R15, R16: 10k; R0603

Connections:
+3V3: CH9.1, CH9.2, M1.VS, M2.VS, M4.VS, M5.VS, R19.2
+ACTR_PWR: C11.+, C12.+, C13.+, C14.+, CH10.2, CH11.2, CH12.2, CH13.2, F4.3 (2), F4.4 (2), R18.2
+ACTR_PWR_INPUT: M5.VIN+1 (VIN+), M5.VIN+2 (VIN+), M5.VIN+3 (VIN+), M5.VIN+4 (VIN+), M5.VIN+5 (VIN+), M5.VIN+6 (VIN+), M5.VIN+7 (VIN+), M5.VIN+8 (VIN+), M5.VIN+9 (VIN+), M5.VIN+10 (VIN+), Q6.4 (D)
+ACTR_SENSING: F4.1, F4.2 (1), M5.VIN-1 (VIN-), M5.VIN-2 (VIN-), M5.VIN-3 (VIN-), M5.VIN-4 (VIN-), M5.VIN-5 (VIN-), M5.VIN-6 (VIN-), M5.VIN-7 (VIN-), M5.VIN-8 (VIN-), M5.VIN-9 (VIN-), M5.VIN-10 (VIN-)
+BATT_INPUT1: F1.3 (2), F1.4 (2), M1.VIN+1 (VIN+), M1.VIN+2 (VIN+), M1.VIN+3 (VIN+), M1.VIN+4 (VIN+), M1.VIN+5 (VIN+), M1.VIN+6 (VIN+), M1.VIN+7 (VIN+), M1.VIN+8 (VIN+), M1.VIN+9 (VIN+), M1.VIN+10 (VIN+), R1.2
+BATT_INPUT1_FUSE: CH1.+, F1.1, F1.2 (1)
+BATT_INPUT2: F2.3 (2), F2.4 (2), M2.VIN+1 (VIN+), M2.VIN+2 (VIN+), M2.VIN+3 (VIN+), M2.VIN+4 (VIN+), M2.VIN+5 (VIN+), M2.VIN+6 (VIN+), M2.VIN+7 (VIN+), M2.VIN+8 (VIN+), M2.VIN+9 (VIN+), M2.VIN+10 (VIN+), R2.2
+BATT_INPUT2_FUSE: CH2.+, F2.1, F2.2 (1)
+BATT_INPUT_SENSING1: C1.1, IC1.17 (V1), M1.VIN-1 (VIN-), M1.VIN-2 (VIN-), M1.VIN-3 (VIN-), M1.VIN-4 (VIN-), M1.VIN-5 (VIN-), M1.VIN-6 (VIN-), M1.VIN-7 (VIN-), M1.VIN-8 (VIN-), M1.VIN-9 (VIN-), M1.VIN-10 (VIN-), Q1.4 (D), R3.2
+BATT_INPUT_SENSING2: C2.1, IC1.16 (V2), M2.VIN-1 (VIN-), M2.VIN-2 (VIN-), M2.VIN-3 (VIN-), M2.VIN-4 (VIN-), M2.VIN-5 (VIN-), M2.VIN-6 (VIN-), M2.VIN-7 (VIN-), M2.VIN-8 (VIN-), M2.VIN-9 (VIN-), M2.VIN-10 (VIN-), Q3.4 (D), R6.2
+PWR_INPUT: C6.1, C8.1, C9.1, C10.1, CH3.2, IC1.15 (VOUT), Q2.4 (D), Q4.4 (D), Q5.3 (S), Q6.3 (S), R13.2, R15.2
+SBC_PWR: CH8.+, F3.3 (2), F3.4 (2), R17.2
+SBC_PWR_INPUT: CH6.2, CH7.2, M3.VIN1 (VIN), M3.VIN2 (VIN), M3.VIN3 (VIN), Q5.4 (D)
+SBC_PWR_OUTPUT: M3.VOUT1 (VOUT), M3.VOUT2 (VOUT), M3.VOUT3 (VOUT), M4.VIN+1 (VIN+), M4.VIN+2 (VIN+), M4.VIN+3 (VIN+), M4.VIN+4 (VIN+), M4.VIN+5 (VIN+), M4.VIN+6 (VIN+), M4.VIN+7 (VIN+), M4.VIN+8 (VIN+), M4.VIN+9 (VIN+), M4.VIN+10 (VIN+)
+SBC_SENSING: F3.1, F3.2 (1), M4.VIN-1 (VIN-), M4.VIN-2 (VIN-), M4.VIN-3 (VIN-), M4.VIN-4 (VIN-), M4.VIN-5 (VIN-), M4.VIN-6 (VIN-), M4.VIN-7 (VIN-), M4.VIN-8 (VIN-), M4.VIN-9 (VIN-), M4.VIN-10 (VIN-)
A-DM: CH9.6, CH10.4
A-DP: CH9.5, CH10.3
B-DM: CH9.8, CH11.4
B-DP: CH9.7, CH11.3
C-DM: CH9.10, CH12.4
C-DP: CH9.9, CH12.3
D-DM: CH9.12, CH13.4
D-DP: CH9.11, CH13.3
G1: C6.2, D1.1 (C), Q1.1 (G), Q2.1 (G), R11.2
G1_: D1.2 (A), IC1.13 (G1), R11.1
G2: C8.2, D2.1 (C), Q3.1 (G), Q4.1 (G), R12.2
G2_: D2.2 (A), IC1.11 (G2), R12.1
GATE_ACTR: C10.2, Q6.1 (G), R15.1, R16.2
GATE_ACTR_: CH5.2, R16.1
GATE_SBC: C9.2, Q5.1 (G), R13.1, R14.2
GATE_SBC_: CH4.2, R14.1
GND: C1.2, C2.2, C3.2, C4.2, C5.2, C7.2, C11.-, C12.-, C13.-, C14.-, CH1.-, CH2.-, CH3.1, CH4.1, CH5.1, CH6.1, CH7.1, CH8.-, CH9.13, CH9.14, CH10.1, CH11.1, CH12.1, CH13.1, IC1.8 (GND), IC1.21 (GND), LED1.C, LED2.C, LED3.C, LED4.C, LED5.C, M1.GND, M2.GND, M3.GND1 (GND), M3.GND2 (GND), M3.GND3 (GND), M3.GND4 (GND), M3.GND5 (GND), M3.GND6 (GND), M4.GND, M5.GND, R5.1, R8.1, R9.1
HYS: IC1.20 (HYS), R9.2
I2C_SCL: CH9.4, M1.SCL, M2.SCL, M4.SCL, M5.SCL
I2C_SDA: CH9.3, M1.SDA, M2.SDA, M4.SDA, M5.SDA
INTVCC: C4.1, IC1.10 (INTVCC), IC1.18 (EN), R10.1
LED_3V3: LED5.A, R19.1
LED_ACTUATOR: LED4.A, R18.1
LED_INPUT1: LED1.A, R1.1
LED_INPUT2: LED2.A, R2.1
LED_SBC: LED3.A, R17.1
OV1: IC1.3 (OV1), R4.1, R5.2
OV2: IC1.5 (OV2), R7.1, R8.2
SHDN: IC1.19 (!SHDN), R10.2
TMR: C3.1, IC1.1 (TMR)
UV1: IC1.2 (UV1), R3.1, R4.2
UV2: IC1.4 (UV2), R6.1, R7.2
VS1: C5.1, IC1.14 (VS1), Q1.3 (S), Q2.3 (S)
VS2: C7.1, IC1.12 (VS2), Q3.3 (S), Q4.3 (S)

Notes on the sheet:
Connecter for SBC Switch
Battery Input No.1 (Priority supply)
LED for checking the operation
Fuse for short circuit (7.5A)
Fuse for short circuit (20A)
KONDO B3M ID: 01~05 + Quad Load Cells to RS-485 Conv. Module
Connecter for Actuators Switch
KONDO B3M ID: 06~09
KONDO B3M ID: 10~14 + Quad Load Cells to RS-485 Conv. Module
KONDO B3M ID: 15~19
Battery Input No.2
Connecters for DC Output (Option)
Connecter for Voltmeter (Option)
1/1
June 12, 2023
SUSTAINA Core Board
Power Input & Sensing
Power Switching
Power Monitor
Power On/Off Switching
Actuator Power & Signal Output
Actuator Signal Input
Single Board Computer's Power Sensing
Actuator's Power Sensing
Power Supply
Power Sensing
<DNP and needs to be shorted.
<DNP
Actual Thresholds by Resistor Network UV: Fall 7V, Rise 7.21V OV: Fall 20.37, Rise 21V

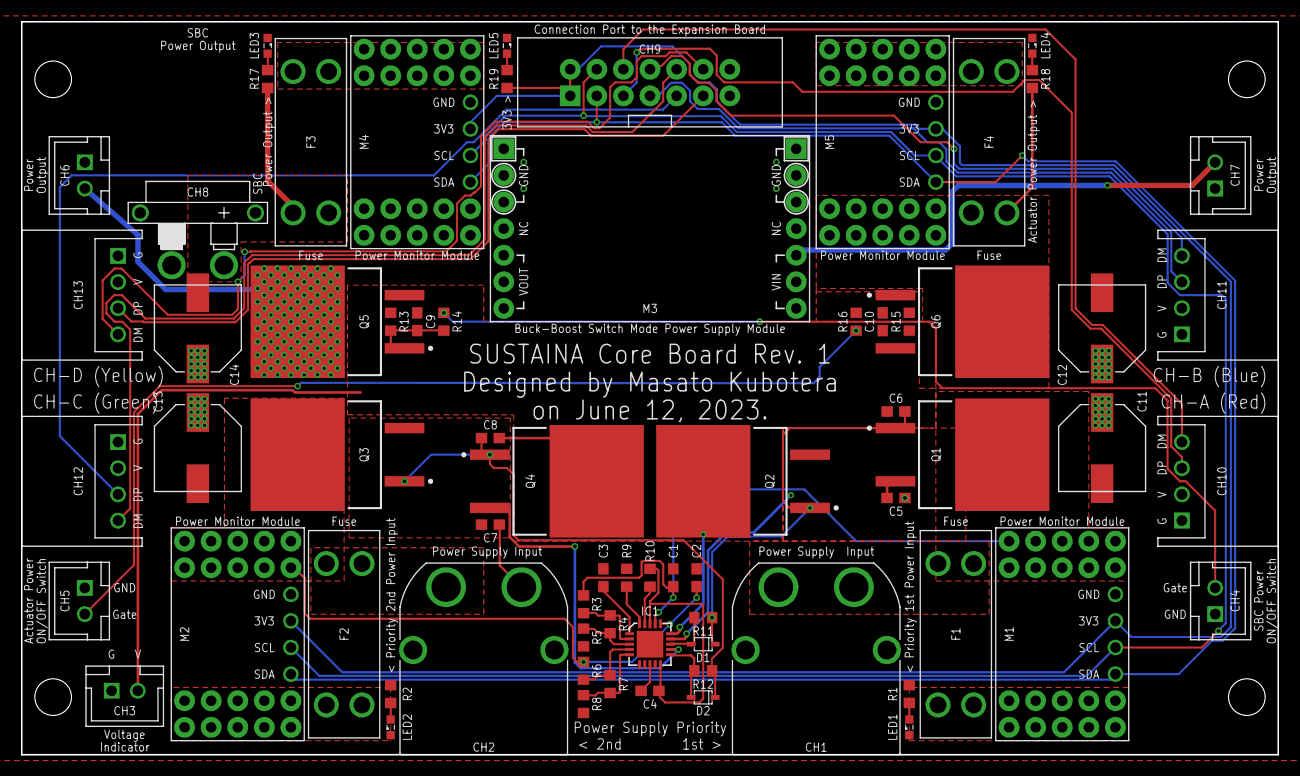
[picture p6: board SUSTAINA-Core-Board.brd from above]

Board: 2 copper layers, 120.0 x 70.0 mm, 69 parts (0 on the bottom side), 49 nets.

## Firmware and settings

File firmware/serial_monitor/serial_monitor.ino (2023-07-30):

#include "./src/INA226.h"
#include "Wire.h"

// number of sensors to be mounted
const int numSensors = 4;

// array of sensor objects
INA226 sensors[numSensors] = {
  INA226(0x40),
  INA226(0x41),
  INA226(0x42),
  INA226(0x43)
};

void setup()
{
  Serial.begin(115200);
  Wire.begin();

  for (int i = 0; i < numSensors; i++)
  {
    if (!sensors[i].begin())
    {
      Serial.println("Could not connect to sensor. Fix and Reboot");
      while (1);
    }
    sensors[i].setMaxCurrentShunt(20, 0.002);
  }
}

void loop()
{
  for (int i = 0; i < numSensors; i++)
    printSensorData(sensors[i]);

  Serial.print("\n \n");
  delay(10);
}

void printSensorData(INA226 & sensor)
{
  Serial.print("ADDRESS: 0x");
  Serial.print(sensor.getAddress(), HEX);
  Serial.print(" \t");

  Serial.print("BUS: ");
  Serial.print(sensor.getBusVoltage(), 5);
  Serial.print(" V\t");

  Serial.print("CURRENT: ");
  Serial.print(sensor.getCurrent_mA(), 5);
  Serial.println(" mA\t");
}

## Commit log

2023-06-07 Initial upload
    [SUSTAINA-Core-Board.brd, SUSTAINA-Core-Board.sch]
2023-06-07 Minimum net thickness changed from 5mil to 8mil
    [SUSTAINA-Core-Board.brd, SUSTAINA-Core-Board.sch]
2023-06-20 Changed board color (Rev 1, 1st order specification)
    [SUSTAINA-Core-Board.brd]
2023-07-25 Upload data for RoboCup2023 competition specifications
    [SUSTAINA-Core-Board.brd, SUSTAINA-Core-Board.sch]
2023-07-30 Added sample programs for multiple voltage and current measurements using Arduino
2023-09-13 Solved the problem of not being able to use a switching power supply in Rev.1
    [SUSTAINA-Core-Board.brd, SUSTAINA-Core-Board.sch]
2023-09-13 Changed the version of schematic to 1.1
    [SUSTAINA-Core-Board.sch]

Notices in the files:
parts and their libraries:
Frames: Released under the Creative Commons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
